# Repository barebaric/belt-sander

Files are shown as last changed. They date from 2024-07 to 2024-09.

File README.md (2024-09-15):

# Mostly Printed Edge Belt Sander

Aug 31st, 2024: The sander is now finished and works successfully for me.
I will add more documentation in the future.

## Project Goals And Design Constraints

In this project I am designing and building an edge belt sander. Design constraints:

* Using only 3D printed components + widely available off-the-shelf hardware (as far as possible) to make it fast and easy to reproduce.

* For belt size 915 x 100 mm (but may offer other configurations in the final release).

* Speed controllable brushless motor.

* Belt change ~~and alignment adjustment~~ with no tools. *I had to compromise, because after adding the electronics there was not enough space for a large belt alignment screw - belt alignment now does require a hex key driver*

* Low profile form factor of less than 14cm - the sander should fit into a drawer when not in use.

* Modular design to allow for customization and faster/cheapter iteration during development.

* Ideally: Option to power from two 18V batteries.

## Checklist And Roadmap For First Release

- [x] Prototype a rough full model to ensure the dimensions fit
  
   - [Version 1](v1)

- [x] Design, test, and refine the lever mechanism for the belt tightener
  
   - Done after testing more than 20 different prototypes: [type 1](fails/disc%20lever), [type 2](fails/slotblock%20lever), [type 3](fails/rotating%20lever)
  
   - [Latest iteration, successfully printed and tested](sander/push%20lever)
     
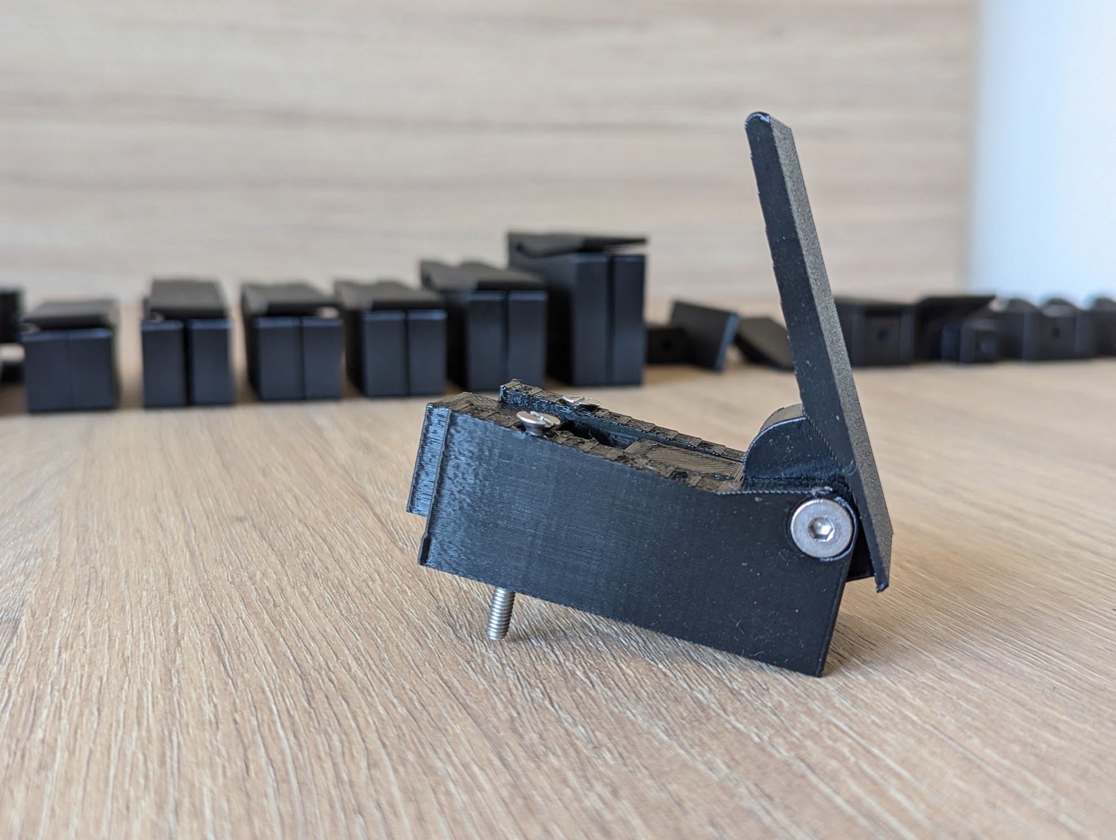
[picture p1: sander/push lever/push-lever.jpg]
Lever designs
     

- [x] Choose a motor
  
   - Dismissed: [997 motor](fails/997%20motor), mostly due to ventilation requirements.
  
   - Dismissed: [Skateboard motor type 1](fails/90%20mm%20skateboard%20motor). Doesn't fit into desired envelope (see design constraints above). It is too long with the shaft included.
  
   - Dismissed: [6384 motor](fails/6384%20motor). Just about fits, but with no space left for routing the cable securely and more expensive because it requires large bearings.
  
   - **Chosen**: [90 mm skateboard motor type 2](components/90%20mm%20skateboard%20motor%20(flat%20type))
     
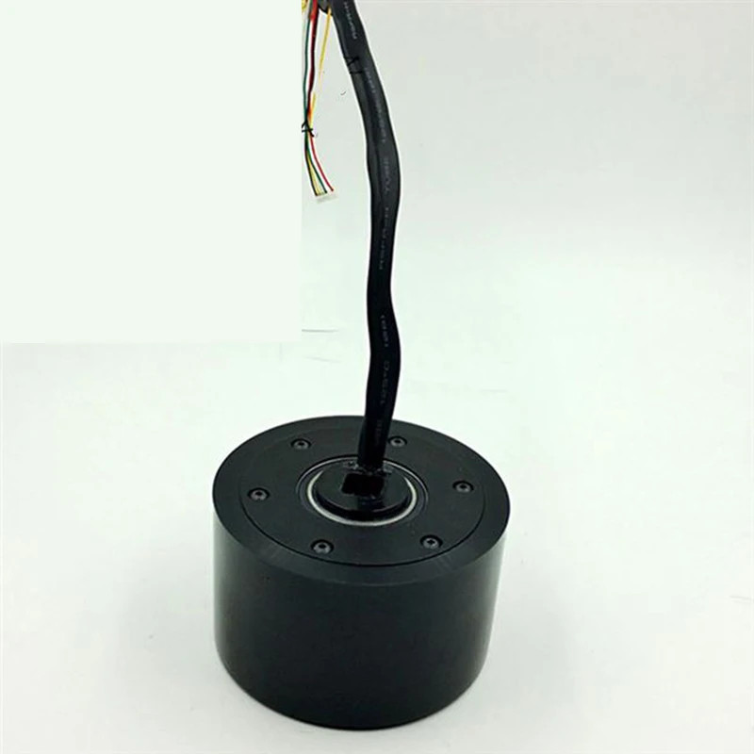
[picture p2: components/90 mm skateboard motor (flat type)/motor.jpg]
Skateboard motor
     

- [x] Choose a BLDC controller
  
   - Dismissed: SNR8503M BLDC controller module for insufficient documentation. Is is also too close to the motor power limit, so may be risky to use anyway.
     
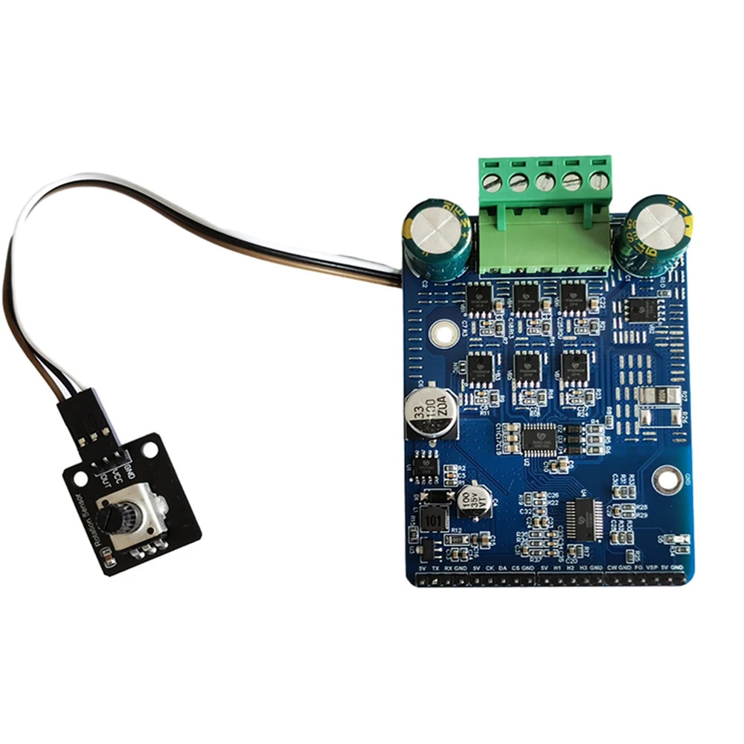
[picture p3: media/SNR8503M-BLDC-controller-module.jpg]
SNR8503M module
     
  
   - Dismissed: ZS-X11D1 module. Power limit too low & documentation insufficient.
     
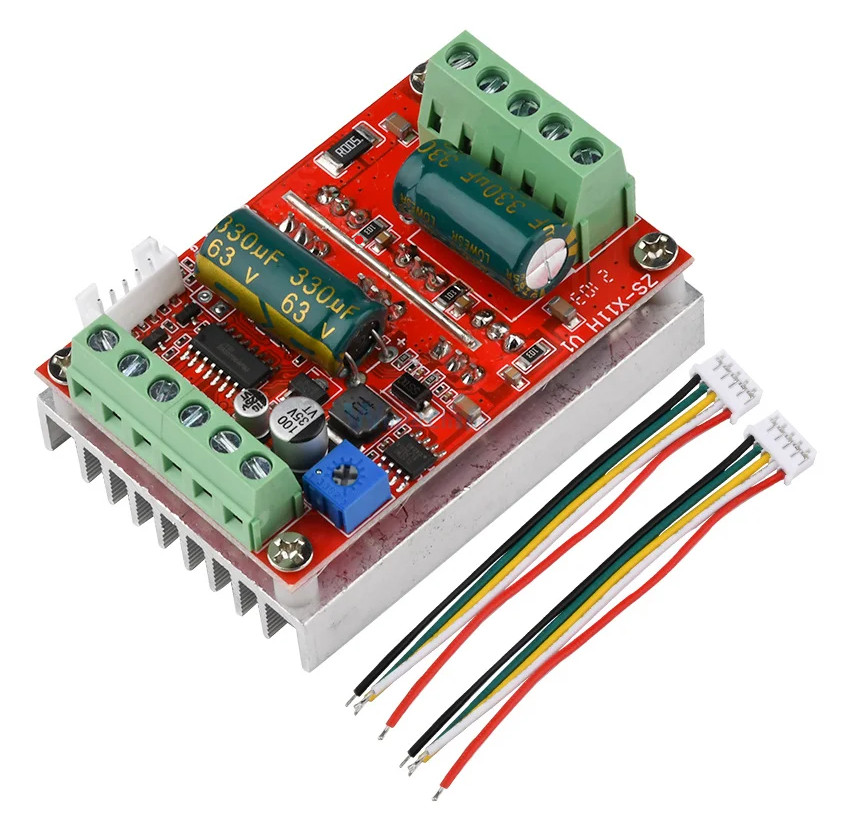
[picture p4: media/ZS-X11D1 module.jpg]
ZS-X11D1
     
  
   - **Chosen**: MKS XDrive (ODrive) Mini
     
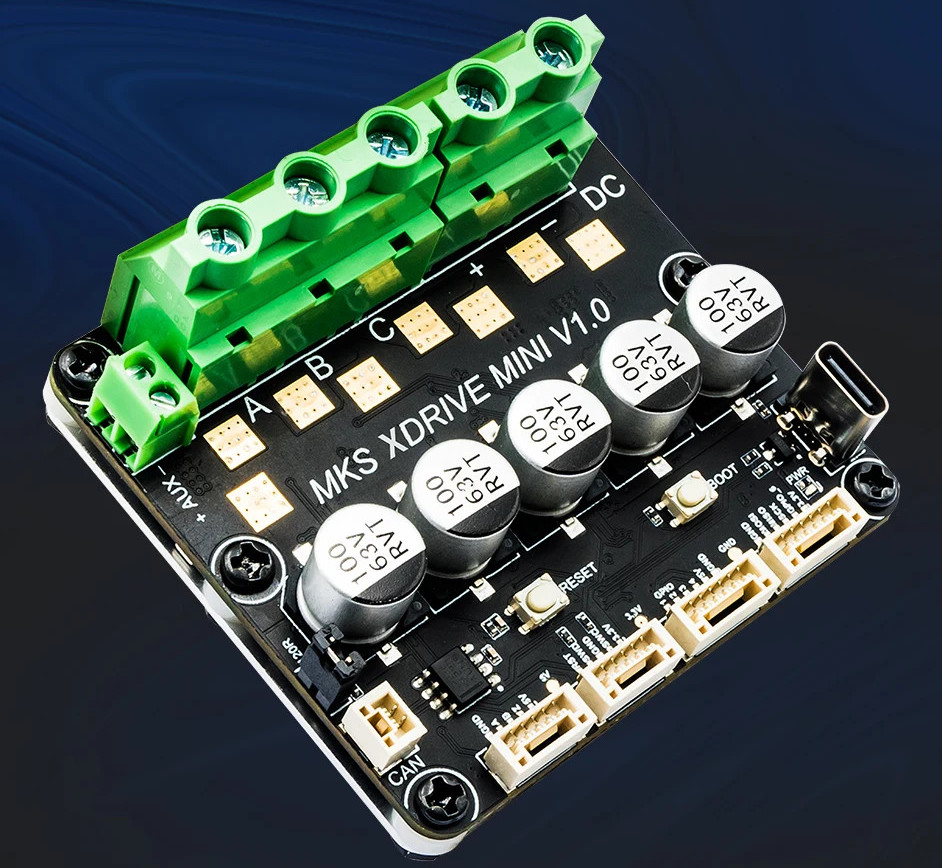
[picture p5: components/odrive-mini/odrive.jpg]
MKS XDrive (Odrive) Mini
     

- [x] Choose a microcontroller
  
   - Dismissed: **NodeMCU ESP8266 with 0.96 display**. Large form factor made panel dimensions too large.
   - Chosen **ESP32 S2 Mini with separate display**.

- [x] Create CAD models for all electronic components
  
   - [x] [90 mm skateboard motor](components/90%20mm%20skateboard%20motor%20(flat%20type))
  
   - [x] [MKS XDrive (Odrive) Mini](components/odrive-mini)
  
   - [x] Brake resistor *(3rd party model found)*
  
   - [x] 10k Potentiometer *(3rd party model found)*
  
   - [x] Power switch *(3rd party model found)*
  
   - [x] [1.3" display](components/1.3%20in%20display)
  
   - [x] Microcontroller *(3rd party model found)*

- [x] Build and test the electronics
  
   - [x] Order parts
  
   - [x] Double check polarity of xdrive connectors, they use red for GND in some cases! (GPIO-connector seems wrong in photos)
     
     *The connector is indeed wrong - red is GND. Be careful.*
  
   - [x] Figure out maximum power draw of VCC pins of ODrive. (Sufficient for microcontroller+display? Otherwise need a separate step down module)
     
     *Should suffice: The XDrive uses an STM32F405RG, which according to its [data sheet](https://www.st.com/resource/en/datasheet/stm32f405rg.pdf) can provide a maximum of 240mA at 3.3v on Vdd.
     The OLED display draws 0.08W = 24.2mA, the ESP8266 has a maximum draw of 170mA and much lower with WiFi disabled. To be safe I'll keep WiFi disabled on the controller.*
  
   - [x] Install Logic Level Converter between ODrive and microcontroller

   - [x] Install Hall sensor filter capacitors

   - [x] Assemble the whole setup

   - [x] Install and test the thermistor

- [x] Software
  
   - [x] Potentiometer to set velocity
  
   - [x] [Configure and test ODrive with motor](components/90%20mm%20skateboard%20motor%20(flat%20type))
  
   - [x] Resolve "ENCODER_ERROR_ILLEGAL_HALL_STATE" issue by adding filter capacitors: [Encoder error ERROR_ILLEGAL_HALL_STATE](https://discourse.odriverobotics.com/t/encoder-error-error-illegal-hall-state/1047/7)
  
   - [x] Figure out microcontroller / ODrive communication. Details of the investigation [documented here](components/odrive-mini/README.md)
  
   - [x] [Temperature sensor](fails/temp-sensor)
  
   - [x] [Display](components/1.3%20in%20display)
  
   - [x] Retrieve and display actual speed from ODrive

   - [x] Actually send the set speed to the controller.

- [x] Design and refine an electronics enclosure module to fit into the sander
  
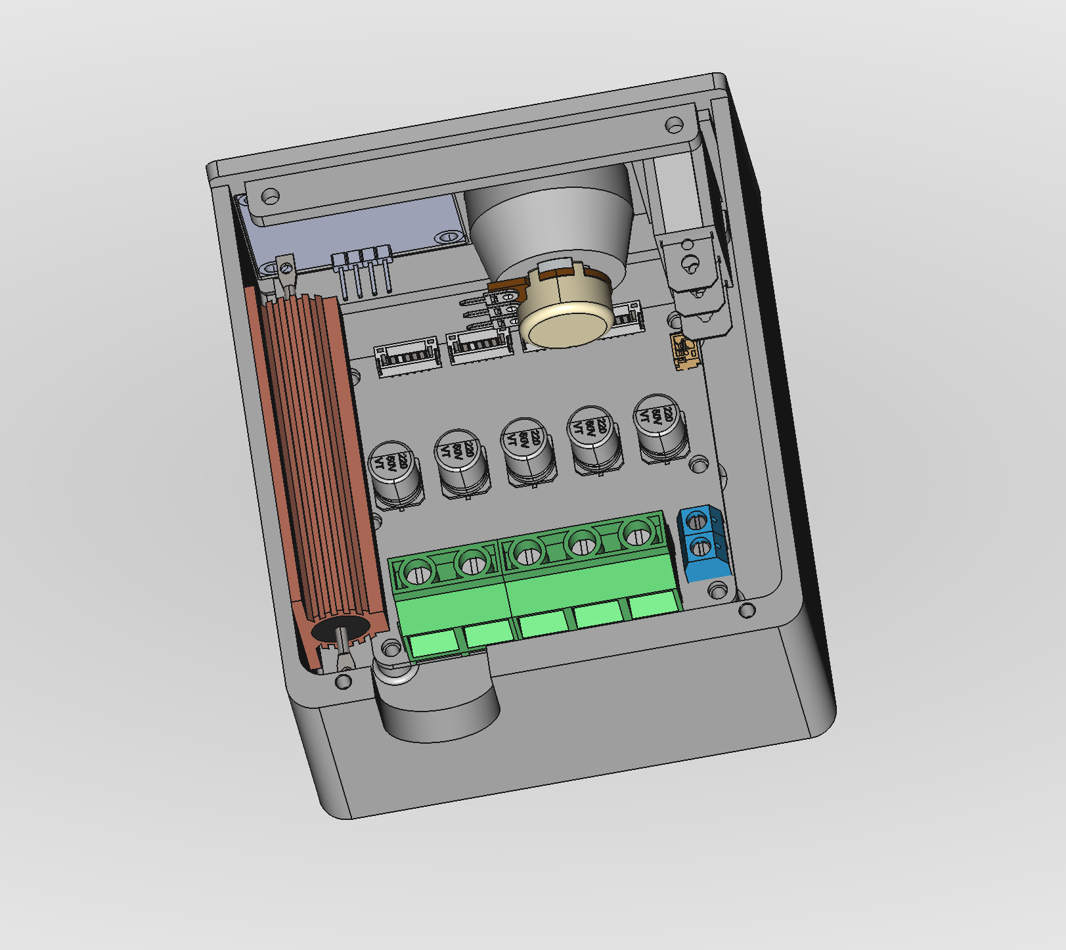
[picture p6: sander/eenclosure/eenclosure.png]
  
  
   - [x] Potentiometer knob
  
   - [x] Panel for display and speed knob.
  
   - [x] Enclosure with mount plate for ODrive Mini and brake resistor.
  
   - [x] Final assembly

- [x] Design and refine hub driven roller with the skateboard motor.
  
   - [x] [Design done](sander/hub).

- [x] Create the new overall assembly tying everything together.
  
   - [x] Fully model the design: *Draft done*
  
   - [x] Create new belt aligner.
  
   - [x] Go through every feature (screws, bearings, etc.) to try and reduce the amount of different hardware needed.
  
   - [x] Check and refine all models.
  
   - [x] Print, test, refine, iterate

- [x] Make a backing plate from steel or aluminium.

- [x] Design and build the final base plate.

## Incorporate lessons learned from V1 prototype

- [x] Provide more clearance (1.5mm on each side?) between rollers and housing, to fit washers on both sides.

- [x] Make left carriage bearing cutouts larger - 23mm probably. It doesn't need tight clearance, as it is pulled to the right anyway.

- [x] Separate the carriage arm from the bracket, make them connectable using screws. For better printability/modularity.

- [x] Make the arm shorter, to make more space for electronics in the unit.

- [x] Recess the tightener knob into the unit. *Knob became obsolete with new lever design*

- [x] Bottom could be 2mm slimmer because it will be seated in a base plate anyway. *Not slimmed down because space was needed for routing the cable in it.*

## Potential extensions after V2

* Dust extraction

* Oscillating unit

* Reduce velocity based on proximity sensor

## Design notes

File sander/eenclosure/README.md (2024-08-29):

# Electronics enclosure

This enclosure is a closed unit that holds all electronics required for the sander, including a control panel with a display.

While it is fully enclosed and could be used as an external/standalone device, it is intended to be inserted into the main sanding unit.

Enclosure

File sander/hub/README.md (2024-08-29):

# Hub with skateboard motor (flat type, without shaft)

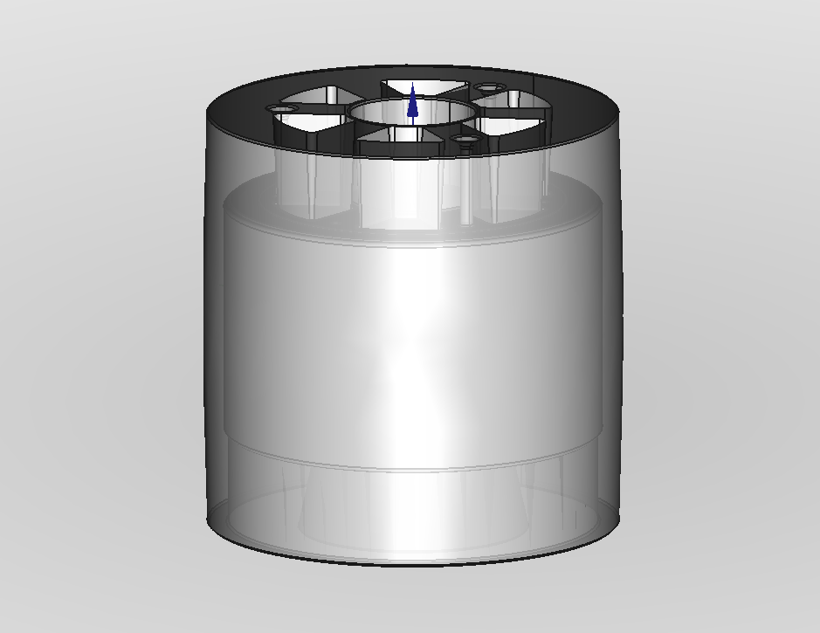
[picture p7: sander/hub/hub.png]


Motor image

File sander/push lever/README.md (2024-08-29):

# Push Lever

This lever is the one that turned out to work best. It uses a spring to apply force to the pin when closed, but removes that pressure when the lever is opened.



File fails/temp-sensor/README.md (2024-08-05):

# Temperature Sensor

Used to monitor motor temperature.

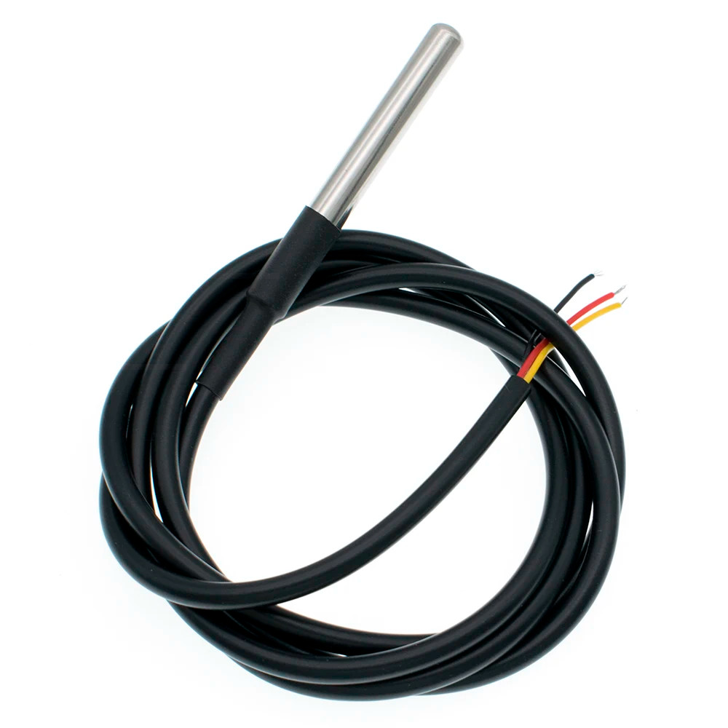
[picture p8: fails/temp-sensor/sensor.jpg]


## Sample code

Found [here](https://beelogger.de/sensoren/temperatursensor-ds18b20/).

```
/*
* (C) 2018 Thorsten Gurzan - beelogger.de
* 
* This program is free software: you can redistribute it and/or modify
* it under the terms of the GNU General Public License as published by
* the Free Software Foundation, either version 3 of the License, or
* (at your option) any later version.
* 
* This program is distributed in the hope that it will be useful,
* but WITHOUT ANY WARRANTY; without even the implied warranty of
* MERCHANTABILITY or FITNESS FOR A PARTICULAR PURPOSE. See the
* GNU General Public License for more details.
* 
* You should have received a copy of the GNU General Public License
* along with this program. If not, see "http://www.gnu.org/licenses/".
*/

// beelogger.de - Arduino Datenlogger für Imker
// Erläuterungen dieses Programmcodes unter https://beelogger.de 

#define ONE_WIRE_BUS 3
#define Anzahl_Sensoren_DS18B20 2 // Anzahl der angeschlossenen Sensoren - Mögliche Werte: '0','1','2',... 

#include "OneWire.h"; 
#include "DallasTemperature.h"; 

#define DS18B20_Aufloesung 12
DeviceAddress DS18B20_Adressen;

OneWire oneWire(ONE_WIRE_BUS); 
DallasTemperature myDS18B20(&oneWire); 

const float No_Val = 999.99;
float Temperatur[Anzahl_Sensoren_DS18B20];   

// Für beelogger-SMD: Aktivierung der Stromversorgung für Sensoren, Module und DS3231 
#define Power_Pin 4

void setup(void) {
  Serial.begin(9600);
  Serial.println("DS18B20 Test");
  Serial.println();
  digitalWrite(Power_Pin, HIGH);
  pinMode(Power_Pin, OUTPUT);
  delay(1000);

  Serial.print("Anzahl aktivierter Sensoren: ");
  Serial.println(Anzahl_Sensoren_DS18B20);

  if ((Anzahl_Sensoren_DS18B20 > 0)) {
    myDS18B20.begin();
    Serial.print("Anzahl angeschlossener Sensoren: ");
    Serial.println(myDS18B20.getDeviceCount(), DEC);
    Serial.println();

    for(byte i=0 ;i < myDS18B20.getDeviceCount(); i++) {
      if(myDS18B20.getAddress(DS18B20_Adressen, i)) {
        myDS18B20.setResolution(DS18B20_Adressen, DS18B20_Aufloesung);
      }
    }

  }
}

void loop(void) {
  if ((Anzahl_Sensoren_DS18B20 > 0)) {
    myDS18B20.requestTemperatures();

    for(byte i=0 ;i < Anzahl_Sensoren_DS18B20; i++) {
      if (i < myDS18B20.getDeviceCount()) {

        Serial.print("Sensor ");
        Serial.print(i+1);
        Serial.print(": "); 

        Temperatur[i] = myDS18B20.getTempCByIndex(i);
        if (Temperatur[i] == DEVICE_DISCONNECTED_C) {
            Temperatur[i] = No_Val;
          Serial.println("Fehler");
        }
        else {
          Serial.print(Temperatur[i]);
          Serial.println(" 'C");
        }
      }
    }

  }
  Serial.println();
  delay(1000);
}
```

## Vendor Description

### Supports second-line and third-line modes

Pluggable terminal waterproof DS18B20 temperature sensor can be used in many places, such as soil temperature detection, hot water tank temperature control, waterproof DS18B20 temperature sensor must also be connected to a pull-up resistor can be used, for which we designed the converter to send use.

### Specifications

Temperature sensor supply voltage: 3.0V ~ 5.5V

Temperature sensor resolution: 9 to 12 adjustable resolution

Temperature range: -55 ~ +125 ° (lead can only withstand the highest temperature of 85 degrees)

Temperature Sensor Output Lead: Yellow (DATA) Red (VCC) and Black (GND)

Adapter Cables: DATA, VCC, BLK,

Suitable platform: for Arduino and Raspberry Pi

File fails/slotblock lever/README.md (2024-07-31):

# Slotblock Lever

## This was an abandoned concept, not in use.

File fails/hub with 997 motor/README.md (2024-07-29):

# Hub with 997 brushed DC motor

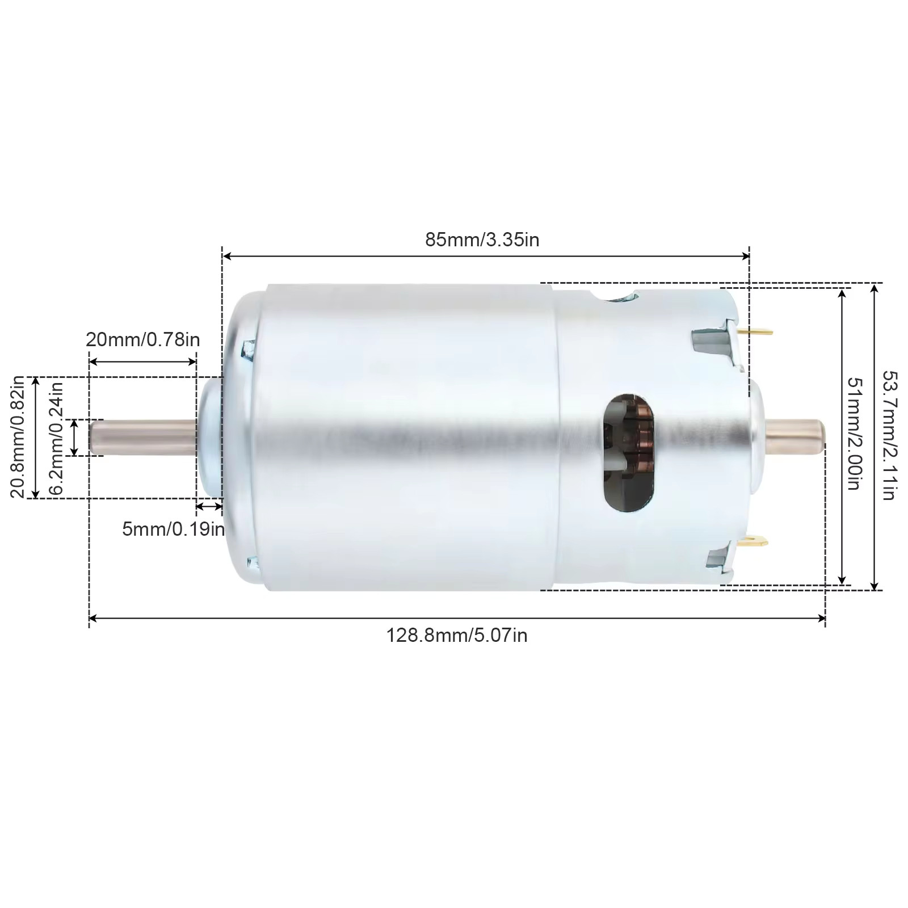
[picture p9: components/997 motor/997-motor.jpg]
Motor image


While this design could work in term of physical constraints, I dismissed it because these brushed motors
get very hot and the design doesn't allow for good enough heat dissipation.

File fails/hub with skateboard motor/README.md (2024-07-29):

# Hub with skateboard motor with shaft

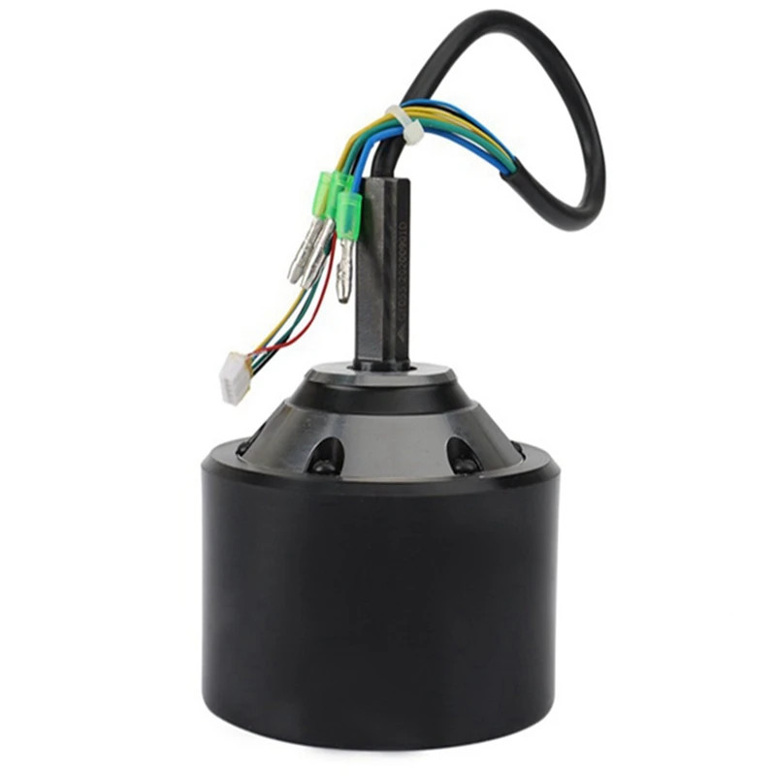
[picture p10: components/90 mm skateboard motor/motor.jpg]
Motor image


This model is only here to prove that this type of motor is unsuitable; the axis stickout is too large.

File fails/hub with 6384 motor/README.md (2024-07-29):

# Hub with 6348 motor

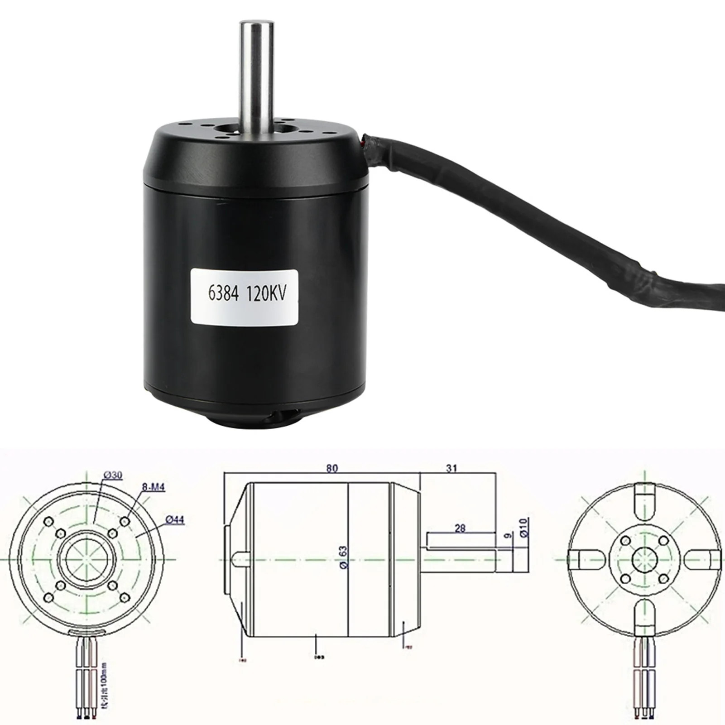
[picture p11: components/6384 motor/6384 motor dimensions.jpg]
6384 motor


This model is another attempt that I dismissed, mainly for cable management reasons:

The cable exits the motor near the shaft at the top; from there, it would need be routed to the bottom.
This isn't great but works - but from there it would also have to be routed underneath the bearing, so a larger bearing is needed
and the required base plate would need to be thicker than the 10mm bearing + cable slot, in total at least 20mm.

I did not want it be be thicker than 12mm, so dismissed this approach.

I also did not like the required 65x85 bearing; it is not as widely available and pricier than I would like.

Another option would be to grind down the shaft and move the motor higher up, but I only want to
use unaltered off-the-shelf parts.

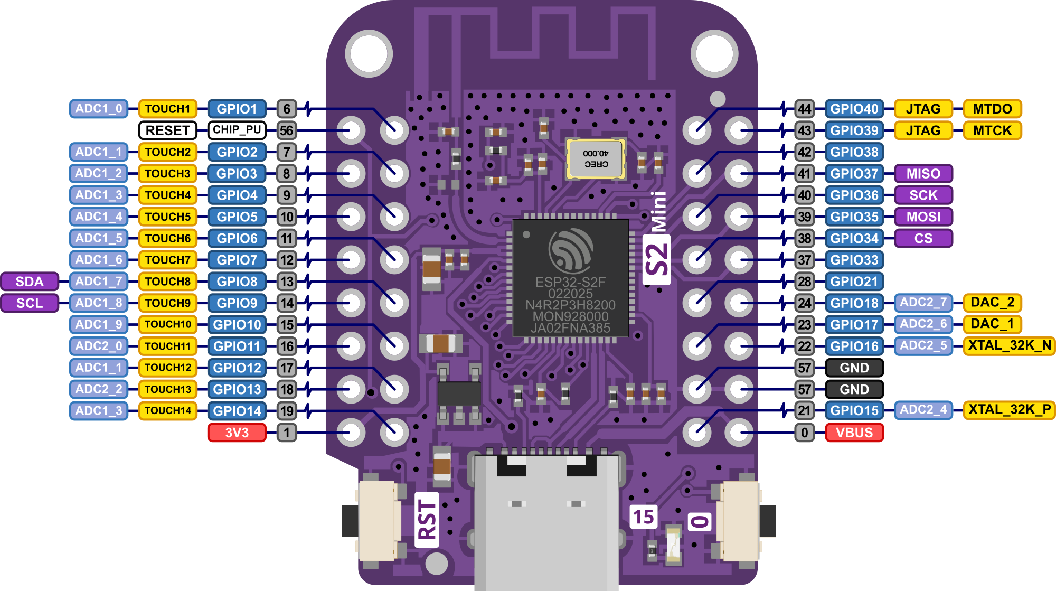
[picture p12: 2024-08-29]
sander/eenclosure/ESP32-S2MiniPinout.png

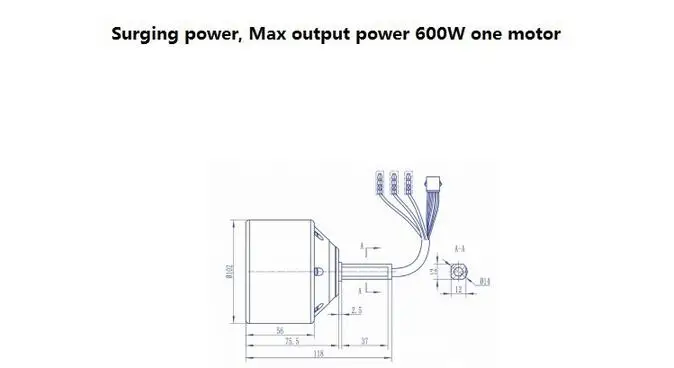
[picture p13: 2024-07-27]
fails/90 mm skateboard motor/dimensions.webp

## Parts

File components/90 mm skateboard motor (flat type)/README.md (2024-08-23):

# Flat skateboard motor

## Data given by supplier (a lot of which turned out to be wrong!)

70mm 90mm Electrical Skateboard 350W 600W Motor Wireless Hub Motor PU Cover for Single Drive or Dual Drive Electrical longboard

- Brake: Yes, the force varies according to speed

- Rated voltage: 24-36V

- Rated power: about 250W

- Top speed: 38km / hour

- 70mm maximum power: 350W

- 90mm maximum power: 600W

- Maximum current: about 38A

- No-load speed: 2640rpm

- No-load current: 500MA

- Efficiency: 85%

- Maximum load: 100KG
1. Use voltage: 24-36V
   2.24 pole stator, smooth start, high torque and high efficiency!
   3.kv value: 110KV (rotation speed of 2640rpm under 24v voltage)
2. The tire can be replaced
3. Closed bearing support at both ends, the whole motor is waterproof and dustproof.
4. Hall supports up to 60V

## Actual data identified

- 24 stator coils

- 28 slots (rotor magnets) = 14 pole pairs

- Hall sensor resolution: 6*pole pairs (=84 cpr)

- Hall sensor bandwidth 100 seems to work ok

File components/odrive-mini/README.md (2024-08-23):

# MKS XDrive Mini (Makerbase, ODrive)

This is the BLDC controller chosen for the belt sander motor.

MKS XDrive Mini

## Status of trying to get this product to work

### Via USB

- Connecting via USB worked with the odrivetool from the supplier repository (linked below). The official odrivetool also worked, but did not offer all configuration names of the old firmware used by the XDrive.

- I was able to make a motor spin correctly in AXIS_STATE_LOCKIN_SPIN mode only. Other modes the motor just did spin, but went into MOTOR_ERROR_DC_BUS_OVER_CURRENT.
  * Note that the hall sensor needs to be calibrated after every(!) reboot of the odrive.
  * odrv0.axis0.requested_state = AXIS_STATE_CLOSED_LOOP_CONTROL
  * odrv0.axis0.controller.config.control_mode=CONTROL_MODE_VELOCITY_CONTROL
  * odrv0.axis0.controller.input_vel = 10
  
  Maybe further hints can be found on [this Chinese website](https://blog.csdn.net/gjy_skyblue/category_10813011.html?spm=1001.2014.3001.5482)

- Under load, the controller went into `ENCODER_ERROR_ILLEGAL_HALL_STATE`. The issue may possibly be resolved by adding filter capacitors: [Encoder error ERROR_ILLEGAL_HALL_STATE](https://discourse.odriverobotics.com/t/encoder-error-error-illegal-hall-state/1047/7)
  * I did just that (used 47nF) and have so far not seen the error anymore.

### Via SPI

I found out that the SPI connector only supports encoders and cannot be used to control the ODrive :-(.

### Via UART

Important: Some versions of the XDrive Mini use 5V logic level on the GPIO pins, while others use 3.3V.
I first got an XDrive with 5V UART voltage, but after that one broke (for an unrelated reason) I ordered
a new one - and was surprised to find that this one sent 3.3V on GPIO, even though the voltage pin on the
same connector still delivered 5V.

That, or perhaps this was the firmware upgrade on the new ODrive. The old one ran 0.5.1, the new one 0.5.6.

If you get the 5V UART version (which you can pretty much only find out using an oscilloscope, a multimeter
won't suffice), then a logic level converter is needed! I used a TXS0108E because I had it at hand and
that worked fine.

Additional collected information:

- I found out that the MKS XDrive Mini has an ancient firmware version 0.5.1, though they also mangled the firmware version number output (shows v0.0.0.dev) so I don't know if they made any other changes.

- In that firmware, you have to connect to the ODrive via USB first, setting `odrv0.config.enable_uart = True` (and saving and rebooting).

- Then, the UART pins are GPIO1 and GPIO2, and they support up to 115200 baud, which worked well.

### Via I2C

Not investigated much yet. There is a setting `odrv0.config.enable_i2c_instead_of_can`, but I am not sure if it is enough to use that - it seems at least the jumper next to the CAN port needs to be removed, too, perhaps more would be needed.

### Via CAN

Unfortunately getting this to work is everything but trivial and specific to the platform you are using. For example, the ESP32-S2 mini that I tried
does not have a direct CAN controller (not to be confused with the CAN transceiver). But it can be used by configuring the onboard TWAI.

But even with your CAN controller working, you still cannot speak ASCII based odrive commands via CAN, since it only supports 8 byte packages.
Instead, a binary format must be used - and there is no library for ODrive yet which implements this.

Therefore I did not use CAN and stuck with UART instead. This has the added benefit that only one connector is needed that
supplies both power and data for my ESP32.

## Firmware update

The firmware can be updated, but not through USB with the odrivetool utility - that one throws UnicodeErrors upon trying.
An st-link adapter is required. I ordered a fake STLink for about 7 Euro and that worked.

However, I first tried to use the open source `st-flash` command line utility (i.e. not the proprietary STCube software),
but the issue is that the required ODrive firmware `ODriveFirmware_v3.6-56V.elf` is provided as .elf file, which
st-flash does not support.
Converting the .elf to .bin is theoretically possible, but this process is architecture specific and therefore non-trivial,
so I gave up and used the proprietary STCube which can be downloaded for free after registration on the ST website.

In STCube it worked without an issue. I followed the instructions from here:

https://ffbeast.github.io/docs/en/software_firmware_flashing.html

## Config

My config is here:

[config.json](config.json)

### Useful commands

In the `odrivetool` CLI utility:

```python
dev0.axis0.requested_state = AXIS_STATE_FULL_CALIBRATION_SEQUENCE
dev0.axis0.requested_state = AXIS_STATE_ENCODER_OFFSET_CALIBRATION
dev0.axis0.requested_state = AXIS_STATE_CLOSED_LOOP_CONTROL
dev0.axis0.controller.input_vel = 2
dump_errors(dev0)
dev0.clear_errors()
dev0.save_configuration()
```

## Supplier provided specs

Supplier doc/firmware repository: [GitHub - makerbase-motor/ODrive-MKS](https://github.com/makerbase-motor/ODrive-MKS)

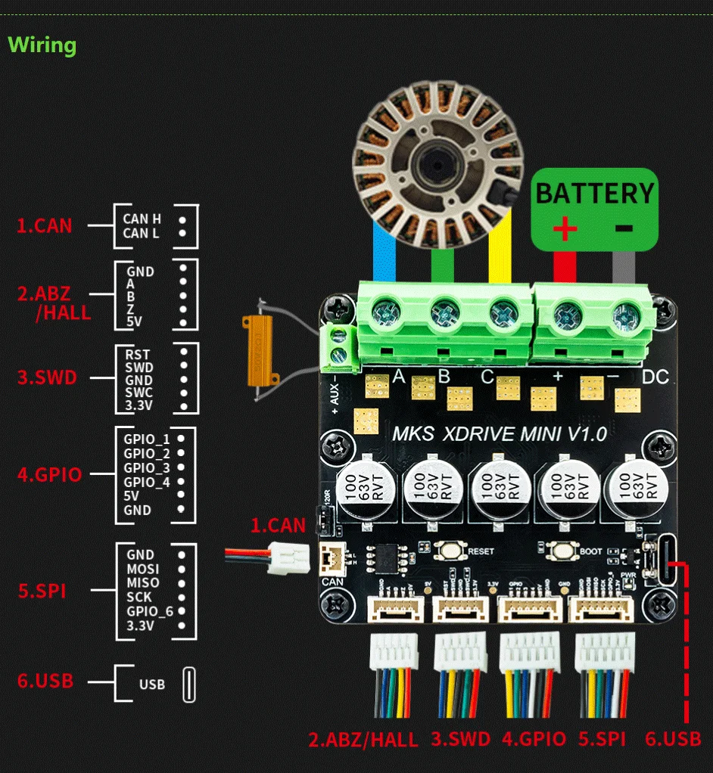
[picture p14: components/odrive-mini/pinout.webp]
Pinout

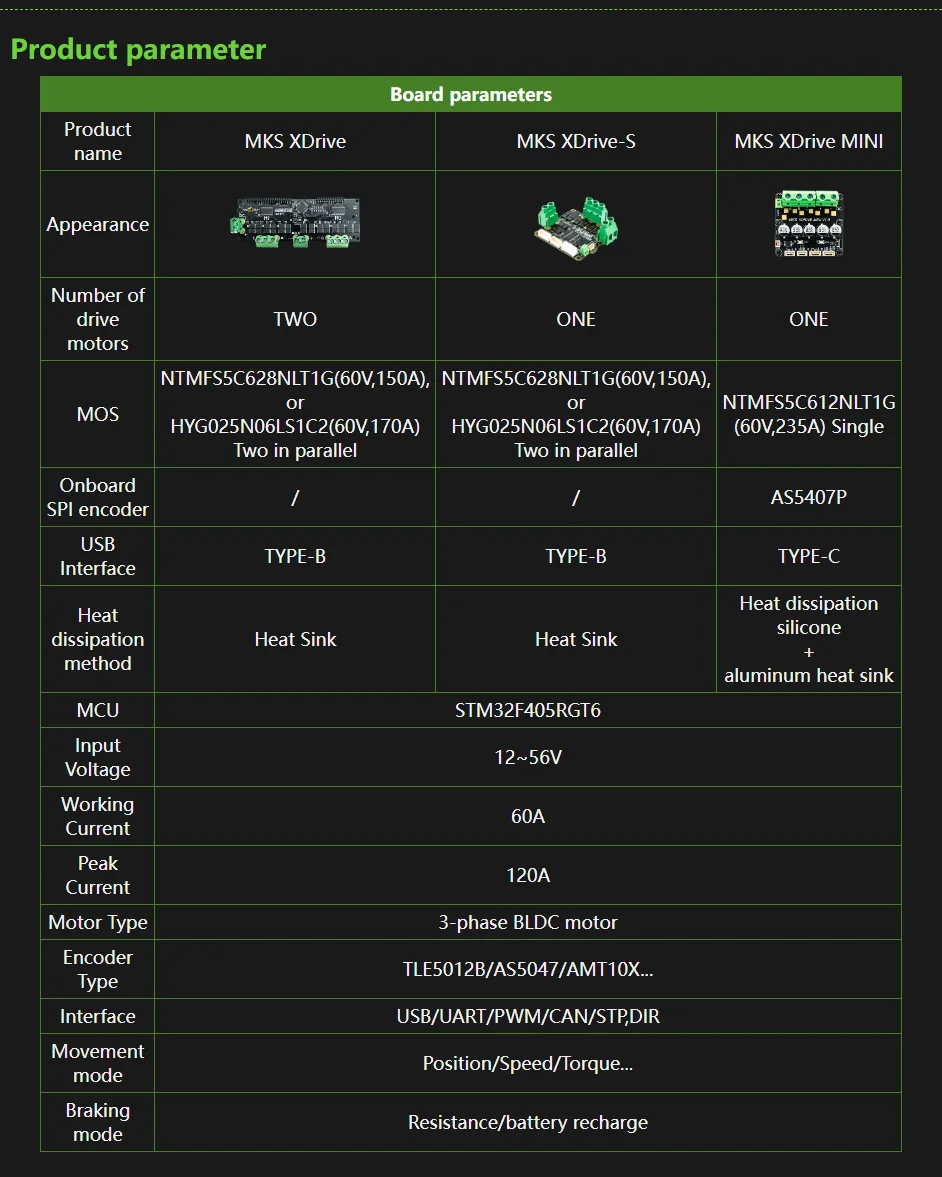
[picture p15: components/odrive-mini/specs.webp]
Specs


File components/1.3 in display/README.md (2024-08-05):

# 1.3" Display

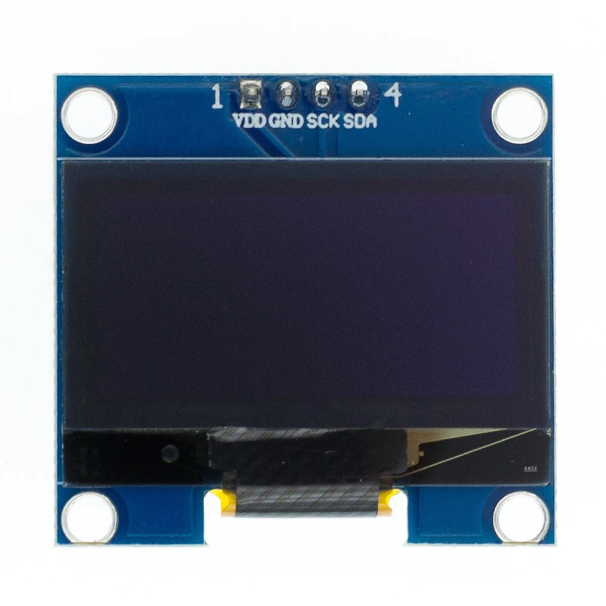
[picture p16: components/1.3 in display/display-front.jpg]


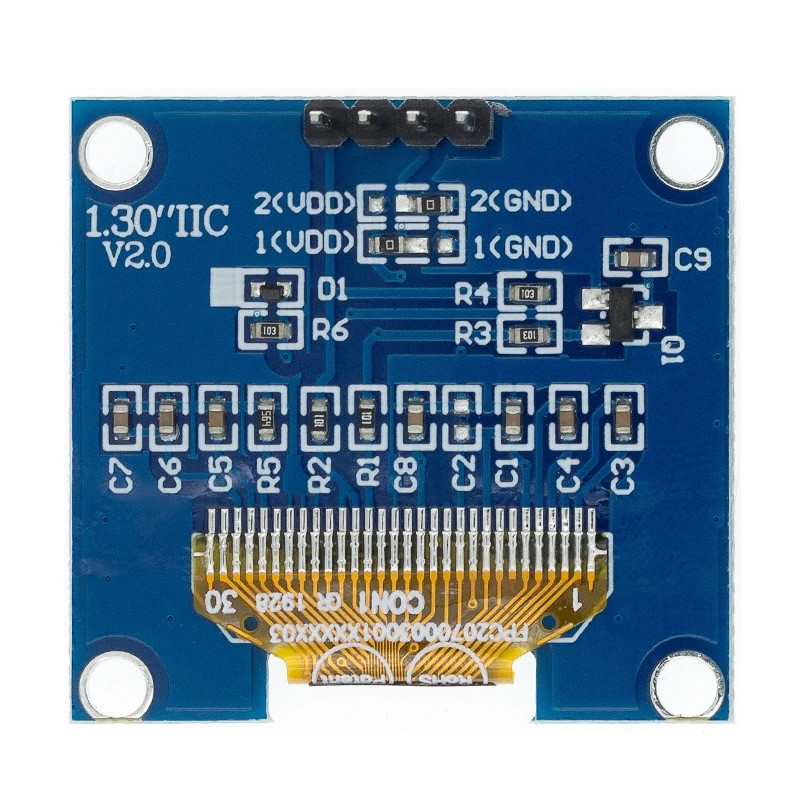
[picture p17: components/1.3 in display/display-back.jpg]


## Vendor Description

* Drive chip SH1106

* Support for multiple operating modes: 3-wire SPI, 4-wire SPI, IIC

* Power supply DC 3V-5V

* Power consumption 0.08W

* Resolution 128x64

* Thickness 4.3 mm

* Size 35.5 x 33.5 mm

* -30 to 70 degrees C

* High-Resolution Display :This 1.3 inch OLED display module offers a high-resolution of 128*64, ensuring clear and sharp visuals for your Arduino projects.

* Versatile Color Options :With its white and blue color drive chip, this LCD module provides vibrant and striking colors, enhancing the aesthetics of your devices.

* IIC I2C Resonate LED :Equipped with IIC I2C resonate LED, this display module ensures smooth and efficient operation, making it ideal for various electronics applications.

* Compact Size :Its compact size of 1.3 inches makes it easy to incorporate into your Arduino projects, offering a sleek and modern look while providing functionality.

* Easy to Use :This LCD module is easy to use, making it perfect for both beginners and experienced users in the electronics field.

* Durable Material :Made from durable materials, this display module is designed to withstand regular use, ensuring long-lasting performance.

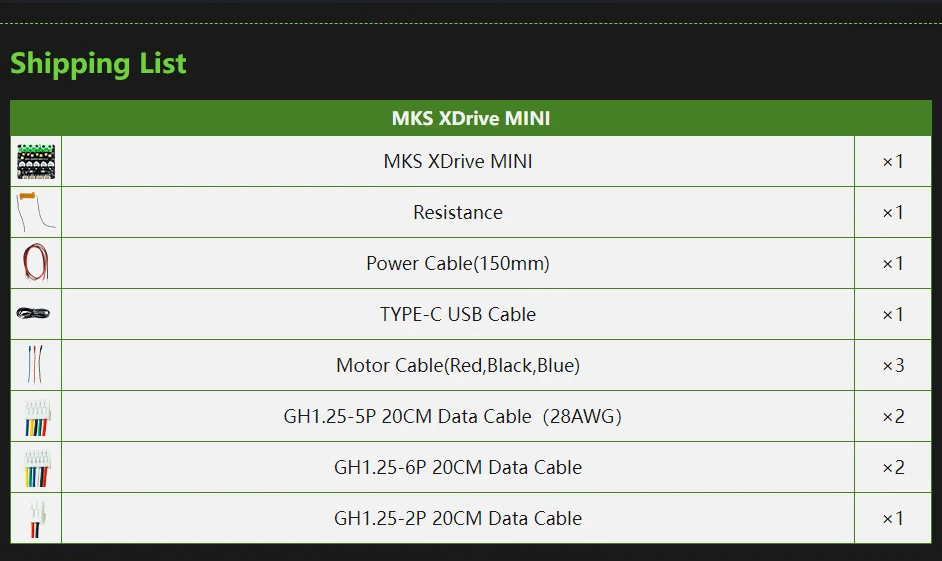
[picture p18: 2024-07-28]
components/odrive-mini/parts-list.webp

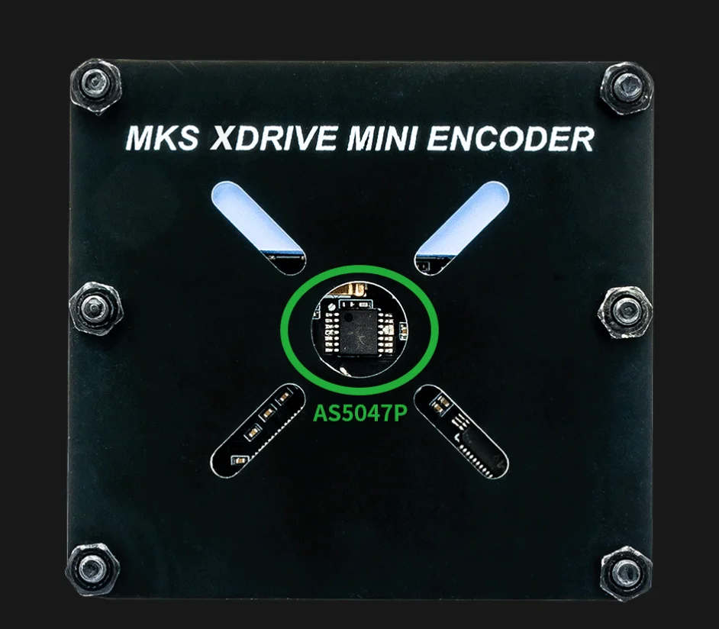
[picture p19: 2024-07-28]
components/odrive-mini/pcb-back.webp

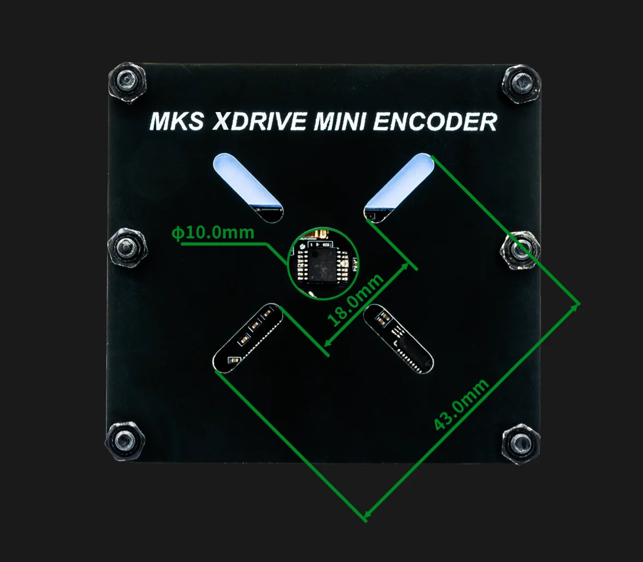
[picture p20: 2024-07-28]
components/odrive-mini/pcb-back dimensions.webp

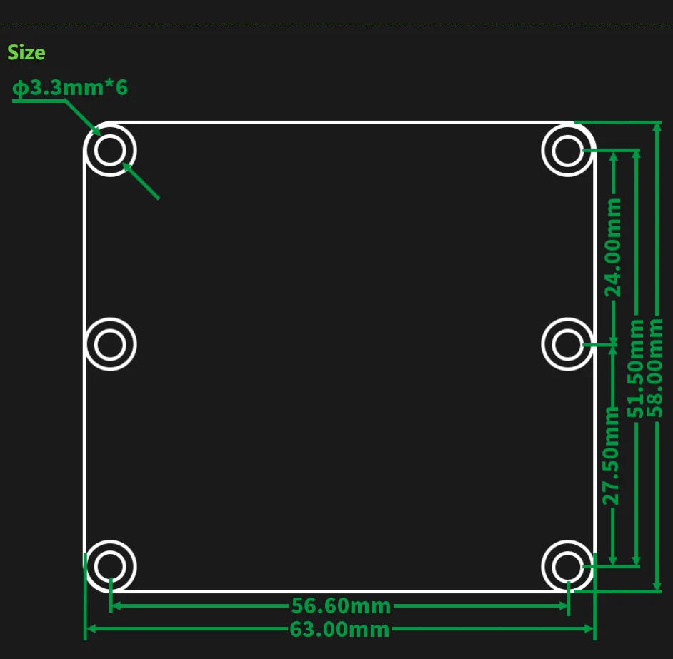
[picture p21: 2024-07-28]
components/odrive-mini/dimensions.webp

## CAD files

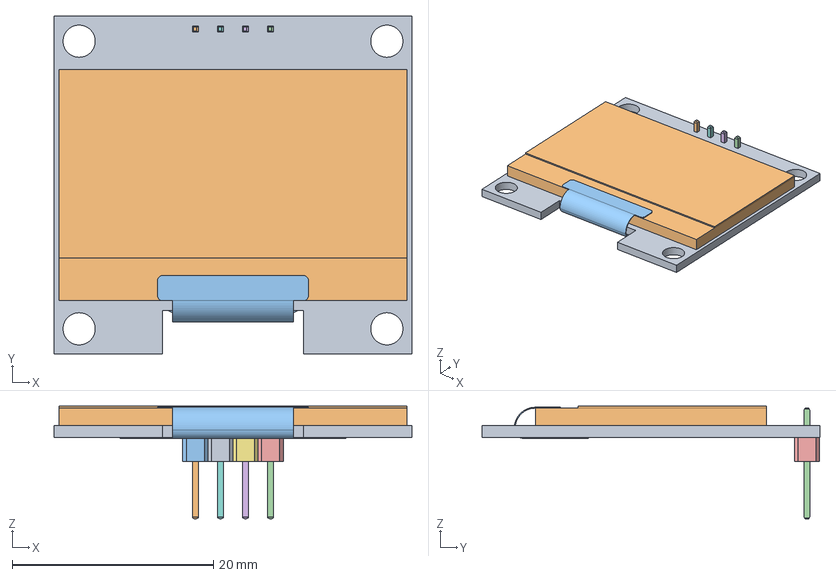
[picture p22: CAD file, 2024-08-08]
components/1.3 in display/display.FCStd
35.6 x 33.6 x 11.2 mm
PCB
OLED
OLED cable
Pin
Pin base
Pin001
Pin base001
Pin002
Pin base002
Pin003
Pin base003

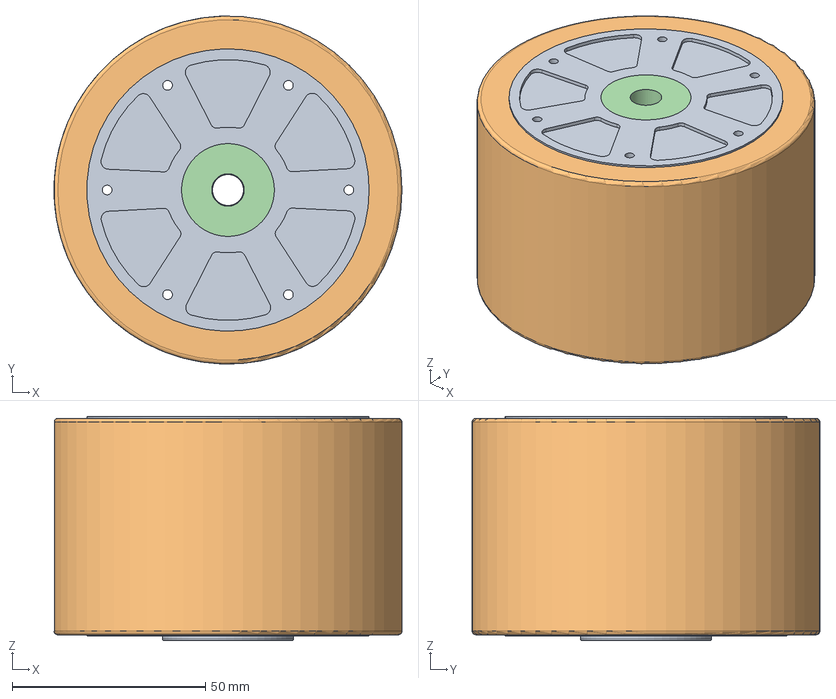
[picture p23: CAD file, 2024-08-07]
components/90 mm skateboard motor (flat type)/skateboard motor (flat type).step
90.0 x 90.0 x 58.0 mm
Rotor
Wheel
Bearing
Stator

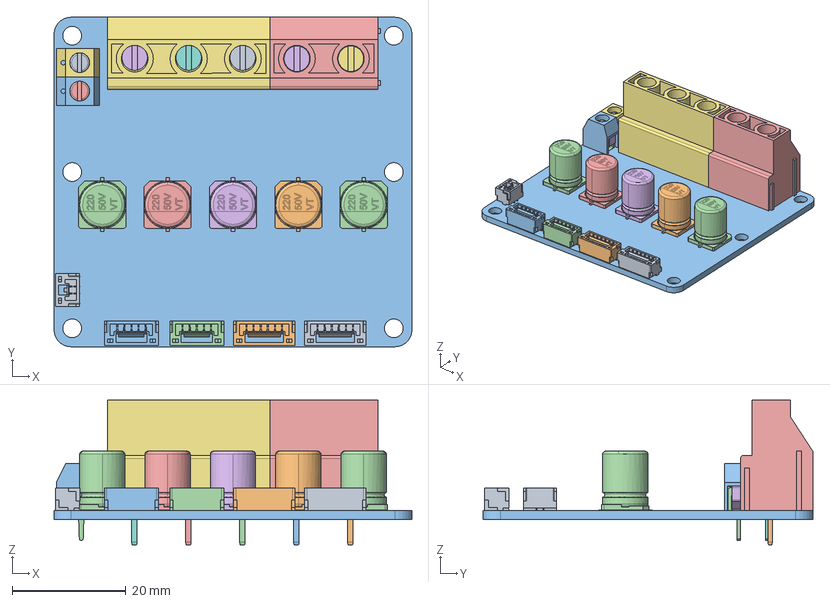
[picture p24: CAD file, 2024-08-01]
components/odrive-mini/MKS ODrive Mini.FCStd
63.0 x 58.0 x 25.5 mm
SM02B-GHS-TB
SM06B-GHS-TB
SM05B-GHS-TB
220uF 50V001
Screw
Screw001
Block
Block001
T003
T004
SM05B-GHS-TB001
220uF 50V002
220uF 50V003
Screw002
Screw003
Block002
Block003
T005
T006
Screw004
SM06B-GHS-TB001
220uF 50V004
Case
Leg
Cap
Case001
Leg001
Cap001
PCB
220uF 50V005

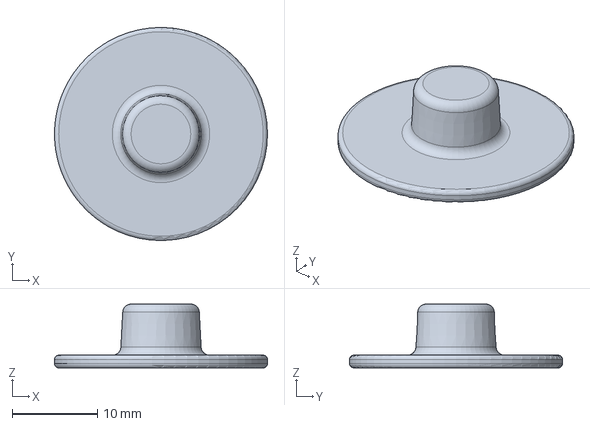
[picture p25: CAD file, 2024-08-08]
components/potentiometer knob/potentiometer knob 25 - flat.FCStd
25.0 x 25.0 x 7.50 mm

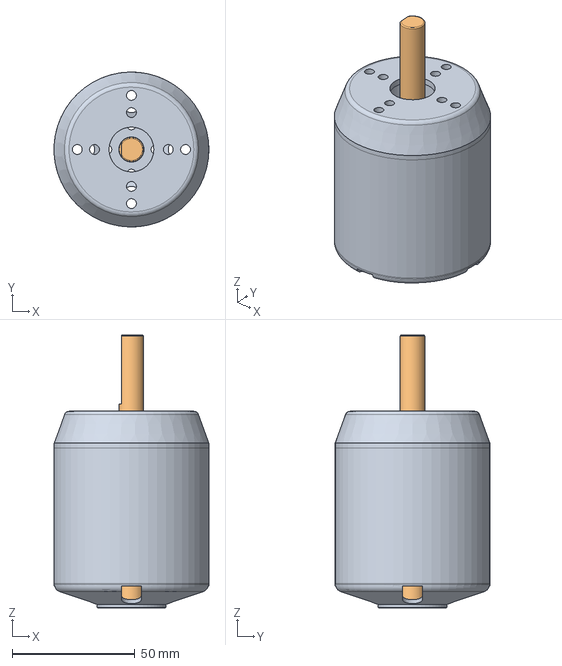
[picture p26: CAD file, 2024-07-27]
fails/6384 motor/6384 DC motor.step
63.0 x 63.0 x 111.0 mm
Axis

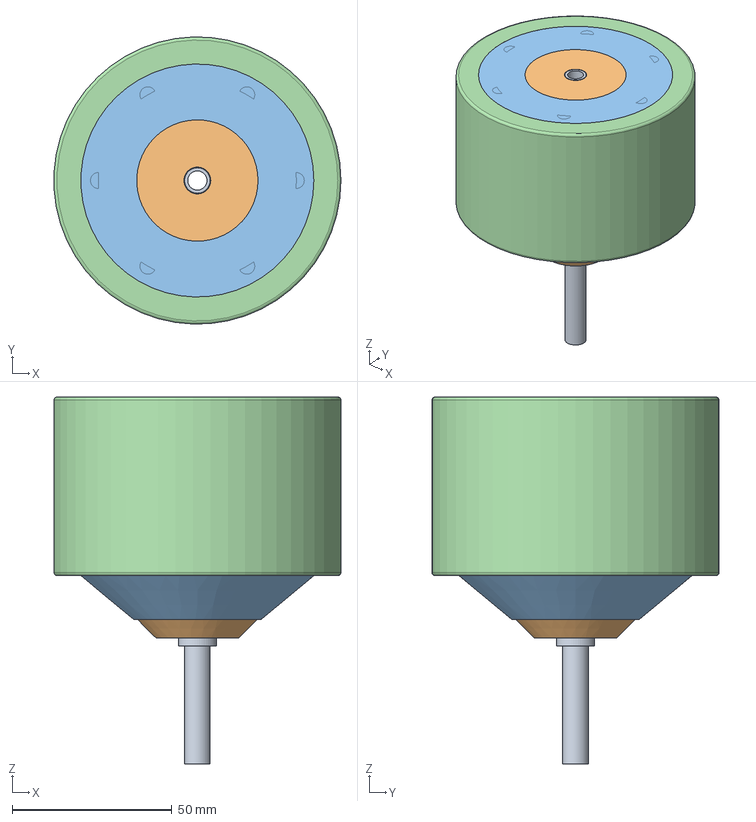
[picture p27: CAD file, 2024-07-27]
fails/90 mm skateboard motor/skateboard motor.step
89.9 x 90.0 x 115.0 mm
Axis
Stator
Outer
Wheel
Bearing

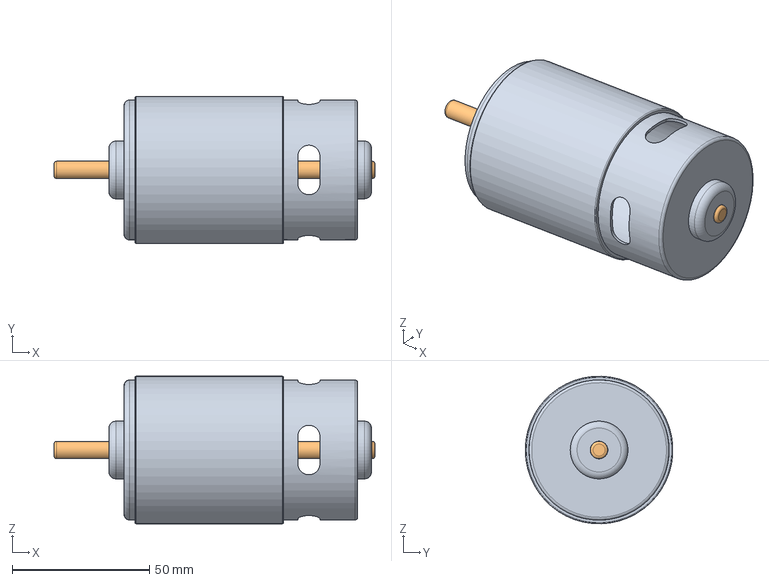
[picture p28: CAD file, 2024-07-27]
fails/997 motor/997 DC motor.step
116.8 x 53.6 x 53.7 mm
Axis

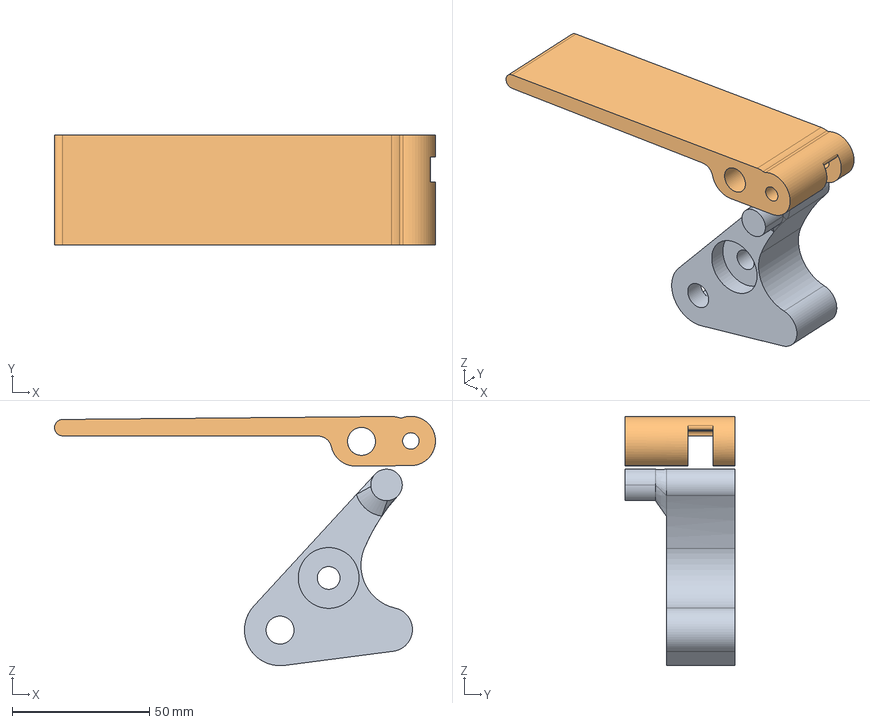
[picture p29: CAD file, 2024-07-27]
fails/disc lever/lever mechanism.FCStd
139.0 x 40.0 x 91.0 mm
AdditiveLoft
Lever

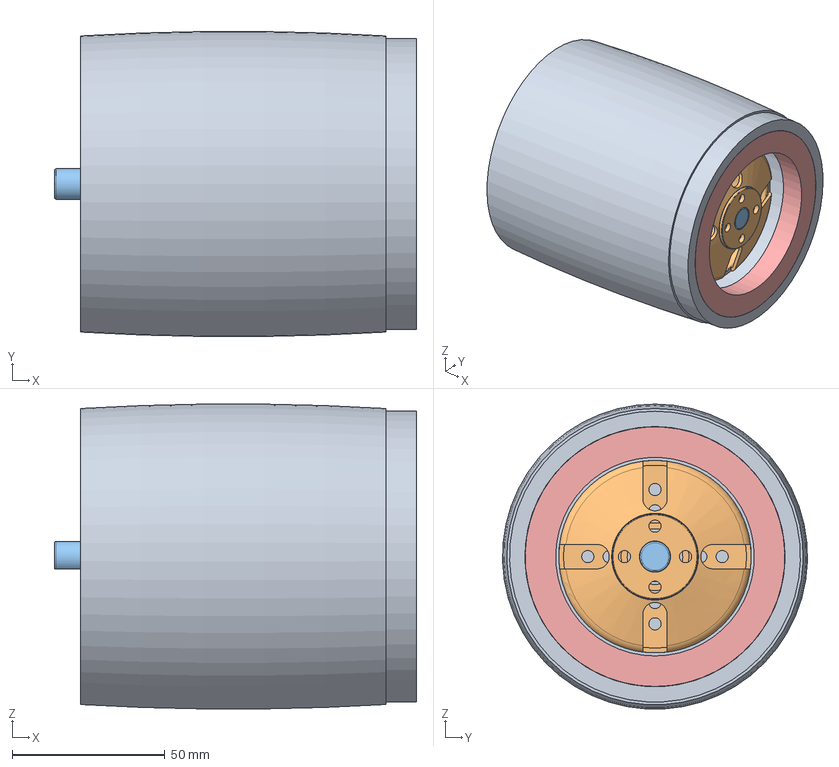
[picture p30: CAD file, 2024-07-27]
fails/hub with 6384 motor/hub 6384.FCStd
118.5 x 99.8 x 99.8 mm
Pulley
Axis
Coupler flange
Bearing

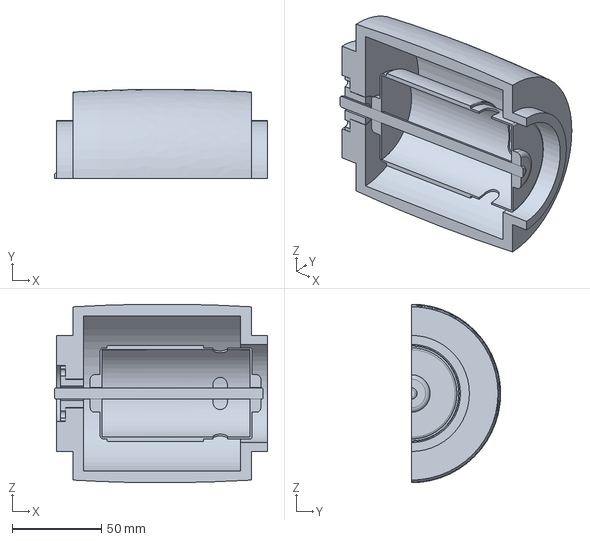
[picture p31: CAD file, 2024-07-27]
fails/hub with 997 motor/hub 997.FCStd
119.2 x 50.0 x 99.9 mm

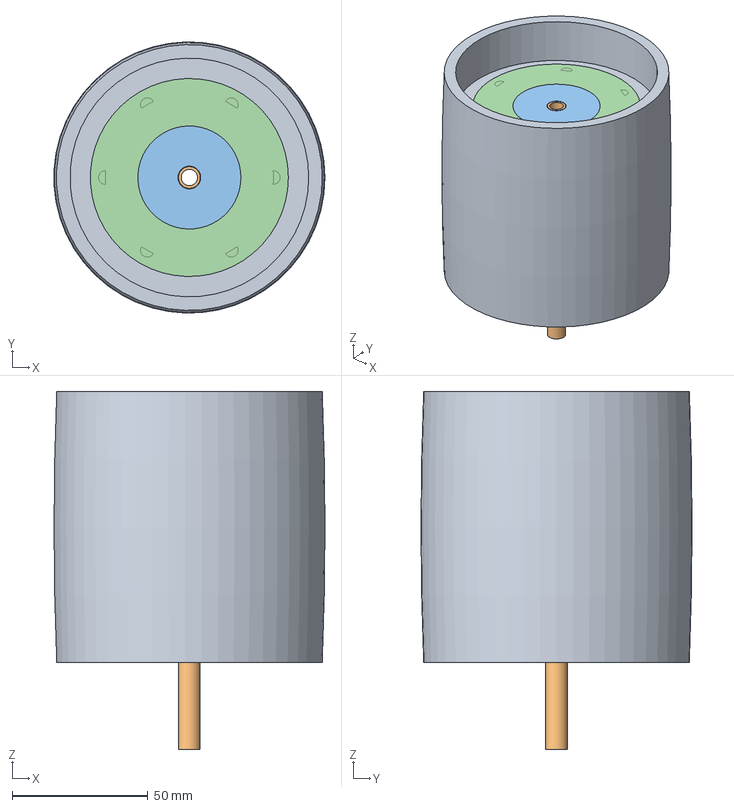
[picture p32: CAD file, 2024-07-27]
fails/hub with skateboard motor/hub with skateboard motor.FCStd
99.9 x 100.0 x 132.0 mm
Corpo
Axis
Stator
Outer
Bearing

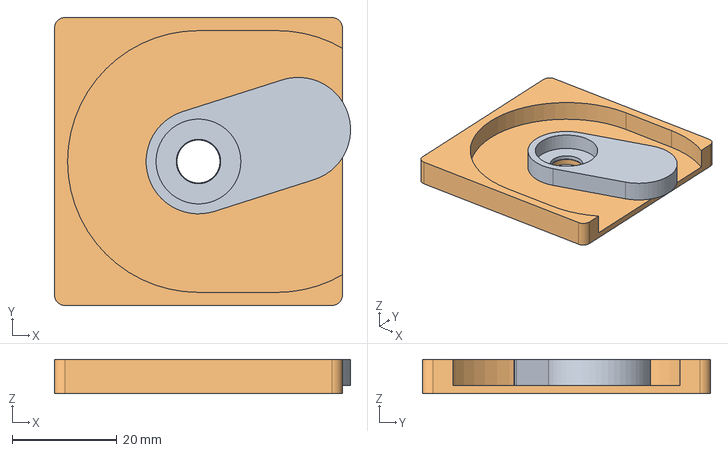
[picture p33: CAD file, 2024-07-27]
fails/rotating lever/rotating lever.FCStd
56.5 x 55.0 x 6.50 mm
Corpo

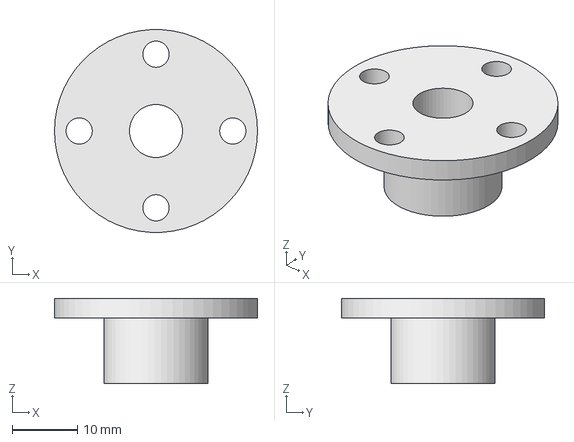
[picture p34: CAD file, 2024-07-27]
fails/Shaft coupler flange/coupler flange-Coupler flange.step
31.0 x 31.0 x 13.0 mm

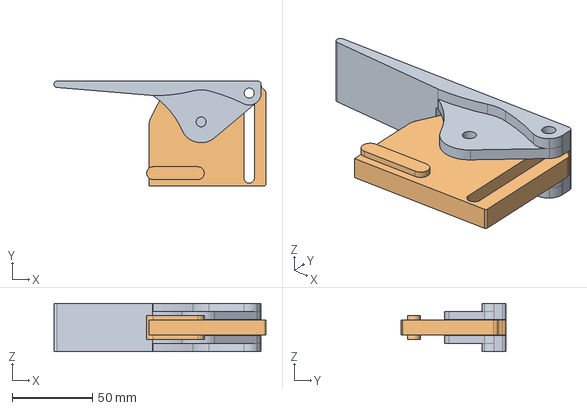
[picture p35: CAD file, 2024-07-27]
fails/slotblock lever/slotblock lever.FCStd
132.4 x 65.5 x 30.0 mm
Lever
Carriage

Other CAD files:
sander/belt sander.FCStd
sander/eenclosure/lid.amf
sander/hub/hub with skateboard motor (flat type).FCStd
sander/push lever/push lever-Lever.amf
components/90 mm skateboard motor (flat type)/skateboard motor (flat type).FCStd
components/potentiometer knob/potentiometer knob 25 - flat.amf
components/potentiometer knob/potentiometer knob 25.FCStd
components/potentiometer knob/potentiometer knob 25.amf
components/potentiometer knob/potentiometer knob 40.FCStd
components/potentiometer knob/potentiometer knob 40.amf
components/potentiometer knob/potentiometer knob 45.FCStd
components/potentiometer knob/potentiometer knob 45.amf
fails/6384 motor/6384 DC motor.FCStd
fails/90 mm skateboard motor/skateboard motor.FCStd
fails/997 motor/997 DC motor.FCStd
fails/Shaft coupler flange/coupler flange.FCStd
sander/belt sander-Base plate template.amf
sander/belt sander-Belt unit base.amf
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

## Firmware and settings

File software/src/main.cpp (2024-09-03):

#include <iostream>
#include <string>
#include <iostream>
#include <Arduino.h>
#include "display.h"
#include "analogpin.h"
#include "thermistor.h"
#include "odrive.h"

#define MOTOR_MAX_SPEED 22

SmoothedAnalogPin potentiometer(A0);
float requested_velocity = 0;  // between 0 and 1.0
float last_velocity = 0;  // between 0 and 1.0
float current_velocity = 0;

Thermistor thermistor(A1, 10000);
float overheat_limit = 75; // Celsius. PETG glassing temp is 85 degrees, adding some margin
float overheat_restart = 65; // Celsius
bool overheated = false;

Display display(T8, T9);
ODrive odrive(T6, T7);

int last_log = 0;
float current_voltage = 0;
String error = "";

TaskHandle_t UITask;
TaskHandle_t MotorTask;

void show_message(String msg) {
    Serial.println(msg);
    display.clearBuffer();
    display.drawString(0, 32, msg.c_str());
    display.sendBuffer();
}

void update_ui() {
    display.clearBuffer();

    // Don't do_log stuff to serial every loop; limit output a bit.
    bool do_log = false;
    if (millis() - last_log > 1000) {
        last_log = millis();
        do_log = true;
    }

    // Write current temperature to the display.
    float temp = thermistor.celsius();
    if (do_log) {
        Serial.print("Temp: ");
        Serial.print(temp);
        Serial.print("°C, ");
        Serial.println(thermistor.raw_value());
    }

    display.drawTemp(temp);
    if (temp > overheat_limit)
        overheated = true;
    if (temp < overheat_restart)
        overheated = false;
    if (overheated) {
        display.drawMessage("Motor too hot!",
                            "Waiting to cool down.");
        return;
    }

    // Display errors, if any.
    if (!error.isEmpty()) {
        display.drawError(error.c_str());
        Serial.print("ERROR, bailing out: \"");
        Serial.print(error);
        Serial.println("\"");
        return;
    }

    // Write current speed to the display.
    // Since the potentiometer value is automatically smoothed,
    // we read twice to speed up the convergence to the selected value,
    // while still benefiting from outlier filtering and smoothing.
    requested_velocity = potentiometer.percent();
    requested_velocity = potentiometer.percent();
    if (do_log) {
        Serial.print("Potentiometer: ");
        Serial.print(requested_velocity);
        Serial.print(", ");
        Serial.println(potentiometer.raw_value());
    }
    display.drawSpeed(requested_velocity);

    // Show status line on display.
    String msg = "Bus: " + String(current_voltage, 1) 
               + "V  Spd: " + String(current_velocity);
    display.drawString(0, 60, msg.c_str());
    if (do_log) {
        Serial.println(msg);
    }

    display.sendBuffer();
}

void ui_loop(void *parameter) {
    for (;;) {
        update_ui();
        vTaskDelay(10 / portTICK_PERIOD_MS);
    }
}

void update_motor_state() {
    // Overheat safehold.
    if (overheated) {
        Serial.println("Motor overheated, going to IDLE");
        odrive.set_axis_requested_state(0, AXIS_STATE_IDLE);
        last_velocity = 0;
        return;
    }

    // Retrieve current state.
    error = odrive.get_errors(0);
    Serial.print("Received errors: ");
    Serial.println(error);
    current_voltage = odrive.get_vbus_voltage();
    Serial.print("Received voltage: ");
    Serial.println(current_voltage);
    current_velocity = odrive.get_current_velocity(0);
    Serial.print("Received velocity: ");
    Serial.println(current_velocity);

    if (!error.isEmpty())
        return;

    // Set velocity.
    float vel_diff = abs(last_velocity - requested_velocity);
    if (vel_diff > 0.02) {
        Serial.print("Sending velocity: ");
        Serial.println(requested_velocity);
        odrive.set_velocity(0, requested_velocity * MOTOR_MAX_SPEED);
        if (requested_velocity < 0.1) {
            Serial.println("Motor going to IDLE");
            odrive.set_axis_requested_state(0, AXIS_STATE_IDLE);
        }
        else if (last_velocity < 0.1 && requested_velocity >= 0.1) {
            Serial.println("Motor going to CLOSED_LOOP_CONTROL");
            odrive.set_axis_requested_state(0, AXIS_STATE_CLOSED_LOOP_CONTROL);
        }
        last_velocity = requested_velocity;
    }
}

void motor_state_loop(void *parameter) {
    for(;;) {
        update_motor_state();
        vTaskDelay(100 / portTICK_PERIOD_MS);
    }
}

void setup() {
    // Initialize serial communication.
    Serial.begin(115200);
    //while (!Serial) {}
    Serial.println("Serial initialized");
    delay(1000);

    // Initialize potentiometer.
    potentiometer.begin();
    requested_velocity = potentiometer.percent();
    Serial.println("Potentiometer initialized");

    // Initialize thermistor.
    thermistor.begin();
    Serial.println("Thermistor initialized");

    // Initialize OLED display.
    display.begin();
    Serial.println("Display initialized");

    // Connect to ODrive controller.
    show_message("Searching motor...");
    odrive.begin();
    Serial.println("ODrive connected");

    // Calibrate motor (ODrive requires this for hall sensor driven motors).
    show_message("Calibrating motor...");
    odrive.calibrate_axis(0);
    Serial.println("Motor calibrated");

/*
    xTaskCreate(
        motor_state_loop,
        "MotorTask",
        2048,
        NULL,
        0,
        &MotorTask);
    xTaskCreate(
        ui_loop,
        "UITask",
        2048,
        NULL,
        1,
        &UITask);
*/
}

void loop() {
    update_motor_state();
    update_ui();
}

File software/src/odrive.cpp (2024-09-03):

#include <SoftwareSerial.h>
#include <type_traits>

#include "util.h"
#include "odrive.h"

// Printing with stream operator. Note that between chars a delay of one ms is added; otherwise ODrive will
// not receive the command reliably. Found a similar problem described here, but in native mode:
// https://discourse.odriverobotics.com/t/odrive-ignores-most-requests-in-uart-native-mode/7368/3
template<class T> inline Print& operator <<(Print &obj,   T arg)         { obj.print(arg);    return obj; }
template<>        inline Print& operator <<(Print &obj, const char *arg) { String a = arg; for (char c : a)   { obj.print(c); delay(1); } return obj; }
template<>        inline Print& operator <<(Print &obj, String arg)      {                 for (char c : arg) { obj.print(c); delay(1); } return obj; }
template<>        inline Print& operator <<(Print &obj, int arg)         { obj.print(arg);    return obj; }
template<>        inline Print& operator <<(Print &obj, float arg)       { obj.print(arg, 4); return obj; }

struct ErrorEntry {
    uint64_t code;
    const char* message;
};

// Error messages
const ErrorEntry axisErrorMessages[] = {
    { AXIS_ERROR_NONE, "No error" },
    { AXIS_ERROR_INVALID_STATE, "Invalid state" },
    { AXIS_ERROR_DC_BUS_UNDER_VOLTAGE, "DC bus under voltage" },
    { AXIS_ERROR_DC_BUS_OVER_VOLTAGE, "DC bus over voltage" },
    { AXIS_ERROR_CURRENT_MEASUREMENT_TIMEOUT, "Current measurement timeout" },
    { AXIS_ERROR_BRAKE_RESISTOR_DISARMED, "Brake resistor disarmed" },
    { AXIS_ERROR_MOTOR_DISARMED, "Motor disarmed" },
    { AXIS_ERROR_MOTOR_FAILED, "Motor failed" },
    { AXIS_ERROR_SENSORLESS_ESTIMATOR_FAILED, "Sensorless estimator failed" },
    { AXIS_ERROR_ENCODER_FAILED, "Encoder failed" },
    { AXIS_ERROR_CONTROLLER_FAILED, "Controller failed" },
    { AXIS_ERROR_POS_CTRL_DURING_SENSORLESS, "Position control during sensorless mode" },
    { AXIS_ERROR_WATCHDOG_TIMER_EXPIRED, "Watchdog timer expired" },
    { AXIS_ERROR_MIN_ENDSTOP_PRESSED, "Min endstop pressed" },
    { AXIS_ERROR_MAX_ENDSTOP_PRESSED, "Max endstop pressed" },
    { AXIS_ERROR_ESTOP_REQUESTED, "Emergency stop requested" },
    { AXIS_ERROR_HOMING_WITHOUT_ENDSTOP, "Homing without endstop" },
    { AXIS_ERROR_OVER_TEMP, "Axis over temperature" },
    { AXIS_ERROR_UNKNOWN_POSITION, "Axis in unknown position" },
    { AXIS_ERROR_UNKNOWN, "Unknown error" }
};

const ErrorEntry motorErrorMessages[] = {
    { MOTOR_ERROR_NONE, "No error" },
    { MOTOR_ERROR_PHASE_RESISTANCE_OUT_OF_RANGE, "Phase resistance out of range" },
    { MOTOR_ERROR_PHASE_INDUCTANCE_OUT_OF_RANGE, "Phase inductance out of range" },
    { MOTOR_ERROR_ADC_FAILED, "ADC failed" },
    { MOTOR_ERROR_DRV_FAULT, "DRV fault" },
    { MOTOR_ERROR_CONTROL_DEADLINE_MISSED, "Control deadline missed" },
    { MOTOR_ERROR_NOT_IMPLEMENTED_MOTOR_TYPE, "Not implemented motor type" },
    { MOTOR_ERROR_BRAKE_CURRENT_OUT_OF_RANGE, "Brake current out of range" },
    { MOTOR_ERROR_MODULATION_MAGNITUDE, "Modulation magnitude out of range" },
    { MOTOR_ERROR_BRAKE_DEADTIME_VIOLATION, "Brake deadtime violation" },
    { MOTOR_ERROR_UNEXPECTED_TIMER_CALLBACK, "Unexpected timer callback" },
    { MOTOR_ERROR_CURRENT_SENSE_SATURATION, "Current sense saturation" },
    { MOTOR_ERROR_CURRENT_LIMIT_VIOLATION, "Current limit violation" },
    { MOTOR_ERROR_MODULATION_IS_NAN, "Modulation is NaN" },
    { MOTOR_ERROR_MOTOR_THERMISTOR_OVER_TEMP, "Motor thermistor over temp" },
    { MOTOR_ERROR_FET_THERMISTOR_OVER_TEMP, "FET thermistor over temp" },
    { MOTOR_ERROR_TIMER_UPDATE_MISSED, "Timer update missed" },
    { MOTOR_ERROR_CURRENT_MEASUREMENT_UNAVAILABLE, "Current measurement unavailable" },
    { MOTOR_ERROR_CONTROLLER_FAILED, "Controller failed" },
    { MOTOR_ERROR_I_BUS_OUT_OF_RANGE, "I bus out of range" },
    { MOTOR_ERROR_BRAKE_RESISTOR_DISARMED, "Brake resistor disarmed" },
    { MOTOR_ERROR_SYSTEM_LEVEL, "System level error" },
    { MOTOR_ERROR_BAD_TIMING, "Bad timing" },
    { MOTOR_ERROR_UNKNOWN_PHASE_ESTIMATE, "Unknown phase estimate" },
    { MOTOR_ERROR_UNKNOWN_PHASE_VEL, "Unknown phase velocity" },
    { MOTOR_ERROR_UNKNOWN_TORQUE, "Unknown torque" },
    { MOTOR_ERROR_UNKNOWN_CURRENT_COMMAND, "Unknown current command" },
    { MOTOR_ERROR_UNKNOWN_CURRENT_MEASUREMENT, "Unknown current measurement" },
    { MOTOR_ERROR_UNKNOWN_VBUS_VOLTAGE, "Unknown VBUS voltage" },
    { MOTOR_ERROR_UNKNOWN_VOLTAGE_COMMAND, "Unknown voltage command" },
    { MOTOR_ERROR_UNKNOWN_GAINS, "Unknown gains" },
    { MOTOR_ERROR_CONTROLLER_INITIALIZING, "Controller initializing" },
    { MOTOR_ERROR_UNBALANCED_PHASES, "Unbalanced phases" }
};

const ErrorEntry encoderErrorMessages[] = {
    { ENCODER_ERROR_NONE, "No error" },
    { ENCODER_ERROR_UNSTABLE_GAIN, "Unstable gain" },
    { ENCODER_ERROR_CPR_POLEPAIRS_MISMATCH, "CPR polepairs mismatch" },
    { ENCODER_ERROR_NO_RESPONSE, "No response" },
    { ENCODER_ERROR_UNSUPPORTED_ENCODER_MODE, "Unsupported encoder mode" },
    { ENCODER_ERROR_ILLEGAL_HALL_STATE, "Illegal hall state" },
    { ENCODER_ERROR_INDEX_NOT_FOUND_YET, "Index not found yet" },
    { ENCODER_ERROR_ABS_SPI_TIMEOUT, "ABS SPI timeout" },
    { ENCODER_ERROR_ABS_SPI_COM_FAIL, "ABS SPI communication failure" },
    { ENCODER_ERROR_ABS_SPI_NOT_READY, "ABS SPI not ready" },
    { ENCODER_ERROR_HALL_NOT_CALIBRATED_YET, "Hall sensor not calibrated yet" }
};

const ErrorEntry controllerErrorMessages[] = {
    { CONTROLLER_ERROR_NONE, "No error" },
    { CONTROLLER_ERROR_OVERSPEED, "Overspeed" },
    { CONTROLLER_ERROR_INVALID_INPUT_MODE, "Invalid input mode" },
    { CONTROLLER_ERROR_UNSTABLE_GAIN, "Unstable gain" },
    { CONTROLLER_ERROR_INVALID_MIRROR_AXIS, "Invalid mirror axis" },
    { CONTROLLER_ERROR_INVALID_LOAD_ENCODER, "Invalid load encoder" },
    { CONTROLLER_ERROR_INVALID_ESTIMATE, "Invalid estimate" },
    { CONTROLLER_ERROR_INVALID_CIRCULAR_RANGE, "Invalid circular range" },
    { CONTROLLER_ERROR_SPINOUT_DETECTED, "Spinout detected" }
};


String errorToString(uint64_t errorMask, const ErrorEntry* errorList, size_t numEntries) {
    String errors = "";

    // Iterate over all possible error codes
    for (uint idx = 1; idx <= numEntries; idx++) {
        ErrorEntry entry = errorList[idx];
        if (errorMask & entry.code) {
            if (!errors.isEmpty())
                errors += ", ";
            errors += entry.message;
        }
    }
    return errors;
}

ODrive::ODrive(uint8_t rx, uint8_t tx) :
  _serial(rx, tx) //RX (ODrive TX), TX (ODrive RX)
{
}

void ODrive::begin() {
    _serial.begin(115200);
    //while (!_serial);
    _serial.setTimeout(200);

    // Say hello.
    while (!get_vbus_voltage()) {
        delay(100);
    }
}

void ODrive::drain() {
    String str = "";
    while (_serial.available()) {
        str += _serial.read();
    }
    /*
    if (str != "")
        Serial << "Drained: " << str << "\n";
    */
}
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

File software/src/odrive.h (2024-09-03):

#ifndef ODRIVE_H
#define ODRIVE_H

#include <SoftwareSerial.h>

enum AxisState {
    AXIS_STATE_UNDEFINED                     = 0,
    AXIS_STATE_IDLE                          = 1,
    AXIS_STATE_STARTUP_SEQUENCE              = 2,
    AXIS_STATE_FULL_CALIBRATION_SEQUENCE     = 3,
    AXIS_STATE_MOTOR_CALIBRATION             = 4,
    AXIS_STATE_ENCODER_INDEX_SEARCH          = 6,
    AXIS_STATE_ENCODER_OFFSET_CALIBRATION    = 7,
    AXIS_STATE_CLOSED_LOOP_CONTROL           = 8,
    AXIS_STATE_LOCKIN_SPIN                   = 9,
    AXIS_STATE_ENCODER_DIR_FIND              = 10,
    AXIS_STATE_HOMING                        = 11,
    AXIS_STATE_ENCODER_HALL_POLARITY_CALIBRATION = 12,
    AXIS_STATE_ENCODER_HALL_PHASE_CALIBRATION = 13
};

// Axis error codes
enum AxisError {
    AXIS_ERROR_NONE = 0x00,
    AXIS_ERROR_INVALID_STATE = 0x01,
    AXIS_ERROR_DC_BUS_UNDER_VOLTAGE = 0x02,
    AXIS_ERROR_DC_BUS_OVER_VOLTAGE = 0x04,
    AXIS_ERROR_CURRENT_MEASUREMENT_TIMEOUT = 0x08,
    AXIS_ERROR_BRAKE_RESISTOR_DISARMED = 0x10,
    AXIS_ERROR_MOTOR_DISARMED = 0x20,
    AXIS_ERROR_MOTOR_FAILED = 0x40,
    AXIS_ERROR_SENSORLESS_ESTIMATOR_FAILED = 0x80,
    AXIS_ERROR_ENCODER_FAILED = 0x100,
    AXIS_ERROR_CONTROLLER_FAILED = 0x200,
    AXIS_ERROR_POS_CTRL_DURING_SENSORLESS = 0x400,
    AXIS_ERROR_WATCHDOG_TIMER_EXPIRED = 0x800,
    AXIS_ERROR_MIN_ENDSTOP_PRESSED = 0x1000,
    AXIS_ERROR_MAX_ENDSTOP_PRESSED = 0x2000,
    AXIS_ERROR_ESTOP_REQUESTED = 0x4000,
    AXIS_ERROR_HOMING_WITHOUT_ENDSTOP = 0x20000,
    AXIS_ERROR_OVER_TEMP = 0x40000,
    AXIS_ERROR_UNKNOWN_POSITION = 0x80000,
    AXIS_ERROR_UNKNOWN = 0xFFFFFFFFF
};

// Motor error codes
enum MotorError {
    MOTOR_ERROR_NONE = 0x00000000,
    MOTOR_ERROR_PHASE_RESISTANCE_OUT_OF_RANGE = 0x00000001,
    MOTOR_ERROR_PHASE_INDUCTANCE_OUT_OF_RANGE = 0x00000002,
    MOTOR_ERROR_ADC_FAILED = 0x00000004,
    MOTOR_ERROR_DRV_FAULT = 0x00000008,
    MOTOR_ERROR_CONTROL_DEADLINE_MISSED = 0x00000010,
    MOTOR_ERROR_NOT_IMPLEMENTED_MOTOR_TYPE = 0x00000020,
    MOTOR_ERROR_BRAKE_CURRENT_OUT_OF_RANGE = 0x00000040,
    MOTOR_ERROR_MODULATION_MAGNITUDE = 0x00000080,
    MOTOR_ERROR_BRAKE_DEADTIME_VIOLATION = 0x00000100,
    MOTOR_ERROR_UNEXPECTED_TIMER_CALLBACK = 0x00000200,
    MOTOR_ERROR_CURRENT_SENSE_SATURATION = 0x00000400,
    MOTOR_ERROR_CURRENT_LIMIT_VIOLATION = 0x00001000,
    MOTOR_ERROR_MODULATION_IS_NAN = 0x00010000,
    MOTOR_ERROR_MOTOR_THERMISTOR_OVER_TEMP = 0x00020000,
    MOTOR_ERROR_FET_THERMISTOR_OVER_TEMP = 0x00040000,
    MOTOR_ERROR_TIMER_UPDATE_MISSED = 0x00080000,
    MOTOR_ERROR_CURRENT_MEASUREMENT_UNAVAILABLE = 0x00100000,
    MOTOR_ERROR_CONTROLLER_FAILED = 0x00200000,
    MOTOR_ERROR_I_BUS_OUT_OF_RANGE = 0x00400000,
    MOTOR_ERROR_BRAKE_RESISTOR_DISARMED = 0x00800000,
    MOTOR_ERROR_SYSTEM_LEVEL = 0x01000000,
    MOTOR_ERROR_BAD_TIMING = 0x02000000,
    MOTOR_ERROR_UNKNOWN_PHASE_ESTIMATE = 0x04000000,
    MOTOR_ERROR_UNKNOWN_PHASE_VEL = 0x08000000,
    MOTOR_ERROR_UNKNOWN_TORQUE = 0x10000000,
    MOTOR_ERROR_UNKNOWN_CURRENT_COMMAND = 0x20000000,
    MOTOR_ERROR_UNKNOWN_CURRENT_MEASUREMENT = 0x40000000,
    MOTOR_ERROR_UNKNOWN_VBUS_VOLTAGE = 0x80000000,
    MOTOR_ERROR_UNKNOWN_VOLTAGE_COMMAND = 0x100000000,
    MOTOR_ERROR_UNKNOWN_GAINS = 0x200000000,
    MOTOR_ERROR_CONTROLLER_INITIALIZING = 0x400000000,
    MOTOR_ERROR_UNBALANCED_PHASES = 0x800000000,
    MOTOR_ERROR_UNKNOWN = 0xFFFFFFFFF
};

// Encoder error codes
enum EncoderError {
    ENCODER_ERROR_NONE = 0x00,
    ENCODER_ERROR_UNSTABLE_GAIN = 0x01,
    ENCODER_ERROR_CPR_POLEPAIRS_MISMATCH = 0x02,
    ENCODER_ERROR_NO_RESPONSE = 0x04,
    ENCODER_ERROR_UNSUPPORTED_ENCODER_MODE = 0x08,
    ENCODER_ERROR_ILLEGAL_HALL_STATE = 0x10,
    ENCODER_ERROR_INDEX_NOT_FOUND_YET = 0x20,
    ENCODER_ERROR_ABS_SPI_TIMEOUT = 0x40,
    ENCODER_ERROR_ABS_SPI_COM_FAIL = 0x80,
    ENCODER_ERROR_ABS_SPI_NOT_READY = 0x100,
    ENCODER_ERROR_HALL_NOT_CALIBRATED_YET = 0x200,
    ENCODER_ERROR_UNKNOWN = 0xFFFFFFFFF
};

// Controller error codes
enum ControllerError {
    CONTROLLER_ERROR_NONE = 0x00,
    CONTROLLER_ERROR_OVERSPEED = 0x01,
    CONTROLLER_ERROR_INVALID_INPUT_MODE = 0x02,
    CONTROLLER_ERROR_UNSTABLE_GAIN = 0x04,
    CONTROLLER_ERROR_INVALID_MIRROR_AXIS = 0x08,
    CONTROLLER_ERROR_INVALID_LOAD_ENCODER = 0x10,
    CONTROLLER_ERROR_INVALID_ESTIMATE = 0x20,
    CONTROLLER_ERROR_INVALID_CIRCULAR_RANGE = 0x40,
    CONTROLLER_ERROR_SPINOUT_DETECTED = 0x80,
    CONTROLLER_ERROR_UNKNOWN = 0xFFFFFFFFF
};


class ODrive {
public:
    // Constructor
    ODrive(uint8_t rx, uint8_t tx);

    // Initialize the connection to the ODrive.
    void begin();

    // Runs the full calibration sequence for the given axis, and waits for it to complete.
    void calibrate_axis(int axis);

    void set_axis_requested_state(int axis, AxisState state);

    AxisState get_axis_state(int axis);

    float get_vbus_voltage();

    void set_velocity(int axis, float vel);

    float get_current_velocity(int axis);

    AxisError get_axis_error(int axis);

    MotorError get_motor_error(int axis);

    EncoderError get_encoder_error(int axis);

    ControllerError get_controller_error(int axis);

    String get_errors(int axis);

private:
    String readString();

    void drain();

    SoftwareSerial _serial;
};

#endif // ODRIVE_H

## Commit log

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2024-07-27 add 997 motor model
    [997 DC motor.FCStd]
2024-07-27 add lever mechanism (WIP)
    [lever mechanism.FCStd]
2024-07-27 redesign lever mechanism
    [lever mechanism.FCStd]
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2024-07-27 tweak lever mechanism again
    [lever mechanism.FCStd]
2024-07-27 rework lever mechanism again
    [lever mechanism.FCStd]
2024-07-27 tweak lever mechanism yet again
    [lever mechanism.FCStd]
2024-07-27 add new lever design (slotblock)
    [slotblock lever.FCStd]
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2024-07-27 add rotating lever (WIP)
    [rotating lever.FCStd]
2024-07-27 one folder per mechanism
    [lever mechanism.FCStd, rotating lever.FCStd, slotblock lever.FCStd]
2024-07-27 add new lever design (push lever)
    [push lever-Lever.amf, push lever-Pushblock.amf, push lever-Spring carriage.amf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]
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2024-07-27 tweak push lever again
    [push lever-Lever.amf, push lever-Pushblock.amf, push lever-Spring carriage.amf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]
2024-07-27 split motor hub into components (motor + coupler flange + hub)
    [997 DC motor.FCStd, 997 DC motor.step, coupler flange-Coupler flange.step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]
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2024-07-27 add skateboard motor component
    [skateboard motor.FCStd]
2024-07-27 add hub with skateboard motor
    [hub with skateboard motor.FCStd, skateboard motor.FCStd, skateboard motor.step]
2024-07-27 add 6384 motor component
    [9384 DC motor.FCStd, 9384 DC motor.step]
2024-07-27 add another hub design attempt using a 6384 brushless motor
    [hub 6384.FCStd]
2024-07-27 improved version of the 6384 based hub
    [hub 6384.FCStd]
2024-07-27 add a new skateboard motor type (flat type)
    [skateboard motor (flat type).FCStd, skateboard motor (flat type).step]
2024-07-28 add hub for flat type skateboard motor
    [hub with skateboard motor (flat type).FCStd]
2024-07-28 add model of MKS ODrive mini
    [MKS ODrive Mini.FCStd]
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2024-07-29 fix 6384 motor filenames
    [6384 DC motor.FCStd, 6384 DC motor.step]
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2024-07-31 some tweaking on potentiometer knob
    [potentiometer knob-Body.amf, potentiometer knob.FCStd]
2024-07-31 minor string change in potentiometer knob model
    [potentiometer knob.FCStd]
2024-07-31 add a panel for display and speed control knob
    [hub 6384.FCStd, hub 997.FCStd, hub with skateboard motor (flat type).FCStd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]
2024-08-01 add odrive mount plate to panel
    [MKS ODrive Mini.FCStd]
2024-08-01 make potentiometer knob slightly smaller
    [potentiometer knob-Body.amf, potentiometer knob.FCStd]
2024-08-01 improve mounting plate stability; use smaller knob
2024-08-01 update panel .amf files
    [mounting-plate.amf, panel.amf]
2024-08-02 fully enclose the electronics
    [enclosure.amf, lid.amf, mounting-plate.amf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]
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2024-08-02 bundle push lever components into a single part
    [push lever.FCStd]
2024-08-02 attempt to remake V2 with newly designed parts, but electronics enclosure is too large
2024-08-02 add potentiomenter knob in 40mm diameter
    [potentiometer knob 40.FCStd, potentiometer knob 40.amf, potentiometer knob 45.FCStd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]
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2024-08-03 finish next iteration of the electronics enclosure
    [eenclosure.FCStd, enclosure.amf, lid.amf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]
2024-08-03 redesign V2 around the new electronics enclosure. still some ways to go
    [eenclosure.FCStd]
2024-08-04 lots of progress on V2: lever and panel mounting solved, better tensioner force transfer, other minor refinements
    [belt sander.FCStd, eenclosure.FCStd, push lever-Spring carriage.amf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]
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2024-08-06 replace power resistor by one received
    [eenclosure.FCStd, enclosure.amf]
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2024-08-07 update hub motor and hub based on dimensions of the motor received
    [hub for skateboard motor (flat type) - base adapter.amf, hub for skateboard motor (flat type) - hub.amf, hub with skateboard motor (flat type).FCStd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]
2024-08-07 some hub and motor refinements
    [hub for skateboard motor (flat type) - base adapter.amf, hub for skateboard motor (flat type) - hub.amf, hub with skateboard motor (flat type).FCStd]
2024-08-07 add cable pocket to hub mount
    [hub for skateboard motor (flat type) - base adapter.amf, hub with skateboard motor (flat type).FCStd]
2024-08-08 3rd party display was not dimensionally accurate; modeled a new one myself
    [display.FCStd]
2024-08-08 add new type of potentiometer knob
    [potentiometer knob 25 - flat.FCStd, potentiometer knob 25 - flat.amf]
2024-08-08 refine panel; panel is now successfully printed and tested
    [panel.amf]
2024-08-08 many refinements for the electronics enclosure
    [enclosure.amf]
2024-08-09 more electronics enclosure tweaks
    [enclosure.amf, panel.amf]
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2024-08-27 fix issues in main assembly caused by previous dev versions of FreeCAD
    [belt sander-Lever transfer arm.amf]
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2024-08-29 remove V1, move files around, add some docs
    [MKS ODrive Mini.FCStd, belt sander - Belt tensioner.amf, belt sander - Belt unit base.amf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]
2024-08-30 show motor/controller/encoder/axis errors, if any
    [main.cpp, odrive.cpp, odrive.h]
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2024-08-31 fix display of errors
    [main.cpp, odrive.cpp, odrive.h]
2024-08-31 more fixxes for error display
    [odrive.cpp]
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2024-08-31 the sander is now finished. adding some refinements for the belt tensioner and aligner
    [belt sander-Belt unit base.amf, belt sander-Belt unit top.amf, belt sander-Small roller holder.amf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]
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2024-09-02 fix: roller holdder missing mounting holes
    [belt sander-Small roller holder arm.amf, belt sander-Small roller holder.amf, belt sander.FCStd]
2024-09-02 fix previous commit
    [belt sander-Small roller holder.amf, belt sander.FCStd]
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2024-09-02 change base mounting holes to make unit mountable with screws from bottom or from top
    [belt sander-Belt unit base.amf, belt sander.FCStd]
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2024-09-03 make tension push block pocket sligthly less deep
    [belt sander-Belt unit top.amf, belt sander.FCStd]
2024-09-03 add CAM job for CNC machining the backing plate
    [belt sander.FCStd]
2024-09-06 fix: missing speed in CNC job for backing plate
    [belt sander.FCStd]
2024-09-15 add printable base plate router template for the sander
    [belt sander-Base plate template.amf, belt sander.FCStd]
2024-09-15 move obsolete components to fails/ and update README
    [6384 DC motor.FCStd, 6384 DC motor.step, 997 DC motor.FCStd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]
2024-09-17 make roller holder slightly longer, and improve placing of adjustment screw
    [belt sander-Small roller holder arm.amf, belt sander-Small roller holder.amf, belt sander.FCStd]
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2024-12-13 add an additional mounting hole on the left side
    [belt sander.FCStd]
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2024-12-14 change small roller holder screws to shorter countersunk ones
    [belt sander-Small roller holder arm.amf, belt sander-Small roller holder.amf, belt sander.FCStd]
2024-12-14 remove bottom mounting hole countersinks, assumption is that unit is mounted from the bottom
    [belt sander-Belt unit base.amf, belt sander.FCStd]
